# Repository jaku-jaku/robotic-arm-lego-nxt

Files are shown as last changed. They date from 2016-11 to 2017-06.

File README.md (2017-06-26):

# RoboticArm_JADO
Built a robotic arm and planetary gearbox system in 3 weeks to handle repetative tasks through joyystick training.

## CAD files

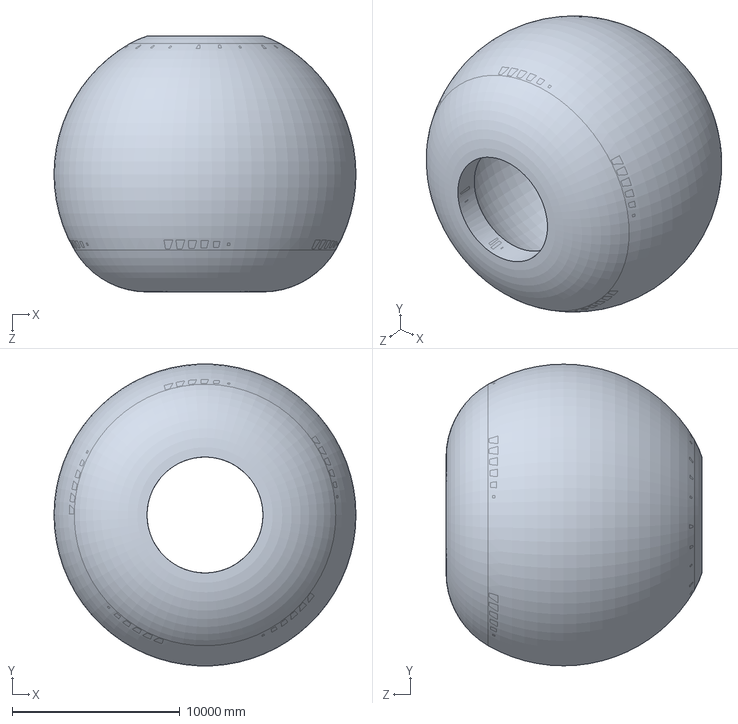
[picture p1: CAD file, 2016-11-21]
SWFiles/Boundaries.SLDPRT
17988.3 x 17970.2 x 15243.4 mm

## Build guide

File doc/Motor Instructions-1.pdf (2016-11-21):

written by Michael Stachowsky and David Lau | Page 1 of 4

# Tetrix Prime Motor Instructions

## GENE 121 – Fall 2015

### Contents

### Introduction

In this course you have access to three different motors:

1. Tetrix Prime Standard Servo – ‘S’ inscribed on servo
2. Tetrix Prime Continuous Rotation Servo – ‘C’ inscribed on servo
3. Lego NXT Motor

In order to drive or control these motors, you can use the Lego NXT brick. The Tetrix Prime servos can also be controlled with the red handheld radio controller.

### Lego NXT Brick Connections

The Tetrix Prime servos must be connected to one of the sensor ports at the bottom of the NXT brick (recommended port: S1). The Tetrix Prime servos require the NXT controller module when connecting to the NXT brick. DO NOT PLUG THE SERVO CONTROLLER INTO A MOTOR PORT, AS THIS WILL DAMAGE THE CONTROLLER (~$75).

Plug the battery pack into SV8 on the servo controller. The black wire is connected to the pin furthest

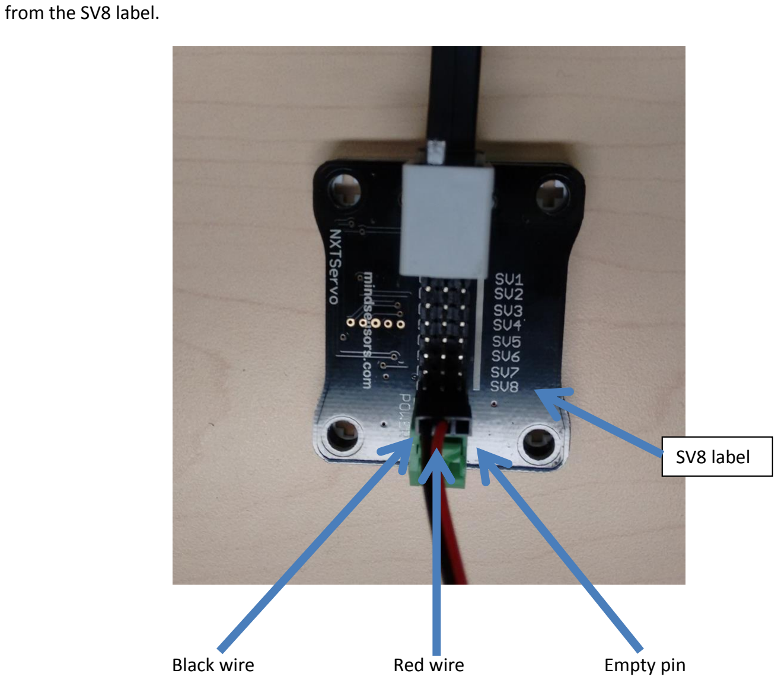
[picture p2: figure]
from the SV8 label.; Black wire; Red wire; Empty pin; SV8 label

### RobotC Code – Tetrix Prime Servos

### Library File

Download the file NXTServo-lib-UW.c into the same folder where you store your RobotC code.

### Setup Code

Your RobotC program should follow the format shown below (assuming you have plugged the interface into S1):

#include "NXTServo-lib-UW.c"

task main()
{
// configure servo controller port SensorType[S1] = sensorI2CCustom9V;

// rest of the code
}

### Continuous Servo Uncalibrated – Usage

Set the speed of the continuous rotation servos (uncalibrated), values range from -100 (counter clockwise rotation) to +100 (clockwise rotation)

setServoSpeed(int nxtPort, int servo_number,
int speed);
e.g.
// servo is plugged in to SV2, set to rotate at 45 setServoSpeed(S1, 2, 45);

// stop servo
setServoSpeed(S1, 2, 0);

### Continuous Servo – Calibration

Plug the servo to be calibrated into the servo controller port SV1. The yellow wire is connected to the pin closest to the SV1 label and the black wire is connected to the pin further from the SV1 label.

Compile and download the ServoDemo.c program to the Lego NXT robot. Run the program.

Using buttons 1 and 2 (right and left buttons) on the Lego NXT brick, increase the servo speed until the servo begins to move. Record the highest servo speed setting for which the servo does not move.

Decrease the service speed until the servo begins to move in the opposite direction. Record the lowest servo speed setting for which the servo does not move.

### Continuous Servo Calibrated – Usage

Set the speed of the continuous rotation servos (calibrated to remove the deadband)

setServoSpeed(int nxtPort, int servo_number,
int speed_setting,
int negative_offset,
int positive_offset);
e.g.
/* servo is plugged in to SV2
deadband (when then motor does not move)
is between -24 and +16
motor is set to run at 10 counts beyond the deadband */
setServoSpeed(S1, 2, 10, -24, 16);

### Standard Servo – Usage

Set the standard servo to a position between -90 degrees and +90 degrees

setServoPosition(int nxtPort, int servo_number,
int position);
e.g.
// servo is plugged in to SV4, set to 30 degrees setServoPosition(S1, 4, 30);

### Gripper – Usage

Set the gripper position from 0 to 70.

setGripperPosition(int nxtPort, int servo_number,
int position);
e.g.
// gripper is plugged in to SV5, partly open, NXT port is S1 setGripperPosition(S1, 5, 25);

To reset the gripper to its neutral position,

resetGripper(int nxtPort,
int servo_number);
e.g.
resetGripper(S1, 5); // gripper is plugged in to SV5

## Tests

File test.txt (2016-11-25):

250 0 -20 0
255 5 -20 0
260 10 -20 0
265 15 -20 0
270 20 -20 0
275 25 -20 0
280 30 -20 0
285 35 -20 0
290 40 -20 0
295 45 -20 0

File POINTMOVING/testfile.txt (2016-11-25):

6
250 0 0 0 0
260 0 0 0 0
270 0 0 0 0
280 0 0 0 0
290 0 0 0 0
300 0 0 0 0

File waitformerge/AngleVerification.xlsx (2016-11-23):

 |  |  | newX | L | alpha1 | numerator | denominator | alpha2 | alpha (rad) | alpha(deg) | alpha(rc) | RobotC Beta
100 | 100 | 100 | 141.4213562 | 173.2050808 | 0.6154797087 | -15840 | -54386.39536 | 1.275263825 | 1.890743534 | 198.3316246 | 108.33 | 45.36
200 | 100 | 100 | 223.6067977 | 244.9489743 | 0.4205343353 | -45840 | -76913.97792 | 0.932297732 | 1.352832067 | 167.5115678 | 77.51 | 77.43
300 | 100 | 100 | 316.227766 | 331.662479 | 0.3062773692 | -95840 | -104142.0184 | 0.4019963086 | 0.7082736778 | 130.5810925 | 40.58 | 126.209
400 | 100 | 100 | 412.3105626 | 424.2640687 | 0.2379411248 | -165840 | -133218.9176 | #NUM! | #NUM! | #NUM! | nan | nan
500 | 100 | 100 | 509.9019514 | 519.6152423 | 0.1936583004 | -255840 | -163159.1861 | #NUM! | #NUM! | #NUM! | nan | nan
 |  |  |  |  |  |  |  |  |  |  |  | 45.36
 |  |  |  |  |  |  |  |  |  |  |  | 45.36
 |  |  |  |  |  |  |  |  |  |  |  | 45.36
 |  |  |  |  |  |  |  |  |  |  |  | 45.36
 |  |  |  |  |  |  |  |  |  |  |  | 77.43
 |  |  |  |  |  |  |  |  |  |  |  | 126.2
 |  |  |  |  |  |  |  |  |  |  |  | nan
 |  |  |  |  |  |  |  |  |  |  |  | nan
 |  |  | numerator | denominator | beta | beta(deg) |  | 103.60 | 0
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

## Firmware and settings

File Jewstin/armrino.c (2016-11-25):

#include "NXTServo-lib-UW.c"
#include "NXT_FileIO.c"

const int GROUND_HEIGHT = -230;
const int FOREARM = 197;
const int SHOULDER = 157;
const int MAX_DIST = SHOULDER + FOREARM;
const int ALPHA_MAX = 150;
const int J3_PHYS_LIM = 90;
const int ALPHA_MIN = 60;
const int NUM_POINTS = 25;
const int GEAR_REDUCTION = 5;
const int FULL_ROTATION_EC = 360 * GEAR_REDUCTION;
const int Basketball=2;
const int Tennisball=3;
const int nothing=1;
const int football=6;

typedef struct
{
	float x , y , z;
	int gP, timeDelay; // timer will be used to control how long arm stays at each point
	bool isValid;
} Point;

typedef struct
{
	float alpha;
	float beta;
	float theta;
} AngleSet;

void readPoint(TFileHandle & in, Point & p0)
{
	readFloatPC(in, p0.x);
	readFloatPC(in, p0.y);
	readFloatPC(in, p0.z);
	readIntPC(in, p0.gP);
}

bool isZValueValid (Point p0)
{
	return (p0.z > GROUND_HEIGHT);
}

bool isWithinRange (Point p0)
{
	return (sqrt(p0.x*p0.x + p0.y*p0.y + p0.z*p0.z))	< MAX_DIST;
}


float calcAlpha(Point & input, float distanceXY, float distancePlane)
{
	float a1 = atan2(input.z,distanceXY);
	float num = (FOREARM*FOREARM) - (SHOULDER*SHOULDER) - (distancePlane*distancePlane);
	float denom = -2.0 * SHOULDER * distancePlane;
	float a2 = acos(num/denom);

	return (180.0/PI)*(a1 + a2 + PI/2.0);
}

float calcBeta(Point & input, float distancePlane)
{
	float num = (distancePlane*distancePlane) - (SHOULDER*SHOULDER) - (FOREARM*FOREARM);
	float denom = -2.0*SHOULDER*FOREARM;

	return (180.0/PI)*(acos(num/denom) - PI); //might inverst PI and acos
}

float calcTheta(Point & input)
{
	return (180.0/PI)*(atan2(input.y,input.x));
}


void calcAngleSet(Point & inputP, AngleSet & outputA)
{
	float distXY = sqrt(inputP.x*inputP.x + inputP.y*inputP.y);
	float distPlanar = sqrt(distXY*distXY + inputP.z*inputP.z);

	outputA.alpha = calcAlpha(inputP,distXY,distPlanar);
	outputA.beta = calcBeta(inputP,distPlanar);
	outputA.theta = calcTheta(inputP);
}

float min (float a, float b)
{
	if (b < a)
	{
		return b;
	}

	return a;
}

float calcMaxBeta (AngleSet & a0)
{
	float beta = 180-a0.alpha;
//	displayString(0,"%0.2f", beta);
	return min(beta, J3_PHYS_LIM);
}

bool anglesValid (AngleSet & a0)
{
	bool output;
	if (a0.alpha <=ALPHA_MAX && a0.alpha >= ALPHA_MIN)
	{

		if (!(a0.beta < calcMaxBeta(a0)))
		{
			eraseDisplay();
		}
		else
		{
			output = true;
		}
	}
	else
	{
		output = false;
	}
	return output;
}

bool isPointValid(Point & p0, AngleSet & a0)
{
	//is point close enough to be able to be reached
	//check z value above the grounnd isZValueValid fun
	bool output = false;

	if (isWithinRange (p0) && isZValueValid (p0))
	{
		calcAngleSet(p0,a0); // calculates all 3 angles

		if (anglesValid (a0) == true)
		{
			output = true;
		}

		//is alpha within range
		//is beta within range
		//if all of the above are okay, then go ahead and move.
	}
	return output;
}
int getEC(){
	int ECvalue=nMotorEncoder[motorA]%FULL_ROTATION_EC;
	//displayString(1,"%f",ECvalue);
	if(ECvalue<0){
		ECvalue+=FULL_ROTATION_EC;
	}
//	displayString(2,"%f",ECvalue);
	return ECvalue;
}
//Testing
int smoothMotionFunc(float index0, int MAXspeed0,int MINspeed0){
	float percent=0;
	if(index0>1){
		percent=1;
	}else
		percent=1/(1+pow(10,(2-4*index0));

	return ((int)((MAXspeed0-MINspeed0)*percent)+MINspeed0);
	//y=1/(1+10^(2-4x))
	//On theory accelerate 0-1 in 0-1
	//and after x=1, y->1
	//so for computation, we do not need to calculate input after x=1
}

int smoothMotion(int curECdif, int initialECDiff){
	int MAXspeed=70,MINspeed=10;
	float index=0, ANGLECHANGE=40;
	//20 degree for changing speed
	index=curECdif;
	if(curECdif>initialECDiff/2.0){
		index=initialECDiff-index;
		//reverse at middle of the action to gain slow down in the end
	}
	index=index/(ANGLECHANGE*5);
//		displayString(2,"%f",index);
	return smoothMotionFunc(index, MAXspeed,MINspeed);
}
void moveJoint1(float ang)
{
	//V1
	//displayString(5,"%i",getEC());
	//int power=20;
	//if(ang<0)
	//	ang+=360;
	//// might need to fix for going backwards direction
	//int targetEC = (int)(ang*FULL_ROTATION_EC/360.0);
	//int forward=1,cw=1;//1 f/ -1 b
	////displayString(6,"%i",targetEC);
	//int diff=targetEC-getEC();

	//	forward=1;
	//	cw=1;
	//	diff=targetEC-getEC();
	//	if(abs(diff)>FULL_ROTATION_EC/2.0){
	//		forward=-1;
	//	}
	//	if(diff>0){
	//		cw=-1;
	//	}
	//		//displayString(7,"%i",getEC())
	//	wait1Msec(2000);
	//	motor[motorA] = -1*power*cw*forward;
 // while(diff!=0){
 // 	diff=targetEC-getEC();
 // 	//displayString(7,"%i",getEC());
 // 	//	while(nNxtButtonPressed!=-1){
	//		//			motor[motorA]=0;
	//		//}

 // 	}
	//motor[motorA] = 0;

///----
	int power=20;
	if(ang<0)
		ang+=360;
	// might need to fix for going backwards direction
	int targetEC = (int)(ang*FULL_ROTATION_EC/360.0);
	int forward=1,cw=1;//1 f/ -1 b
	//displayString(6,"%i",targetEC);
	int diff=targetEC-getEC();
	int initDiff=diff;
	//	displayString(7,"%i",getEC());
	//	wait1Msec(2000);
	while(diff!=0){
		forward=1;
		cw=1;
		if(abs(diff)>FULL_ROTATION_EC/2.0){
			forward=-1;
		}
		if(diff>0){
			cw=-1;
		}
			//displayString(7,"%i",getEC());
			power=smoothMotion(fabs(initDiff-diff),fabs(initDiff));
		motor[motorA] = -1*power*cw*forward;
  	diff=targetEC-getEC();
  //	displayString(7,"%i",getEC());
  	if(diff==0){
  			motor[motorA] = 0;
  			//wait1Msec(200);
  			//diff=targetEC-getEC();//PD not working
  	}
  }
	motor[motorA] = 0;

	////----

	//if (targetEC > nMotorEncoder[motorA])
	//{
	//	motor[motorA] = 40;
	//	while(nMotorEncoder[motorA] < targetEC) {}
	//}
	//else if (targetEC < nMotorEncoder[motorA])
	//{
	//	motor[motorA] = -40;
	//	while (targetEC > nMotor
	//}






	//motor[motorA] = 40;
	//while (nMotorRunState[motorA] != runStateIdle) {}
	//motor[motorA] = 0;
}

void moveJoint2(float ang)
{
	setServoPosition(S4, 1, 0.0014*ang*ang +1.5288*ang - 173.79 );   // QUAD: 0.0014*ang*ang +1.5288*ang - 173.79
}

void moveJoint3(float ang)
{
	setServoPosition(S4, 2, -0.0007*ang*ang + 0.9882*ang + 21.773); // -0.0007*ang*ang + 0.9882*ang + 21.773
}

void moveRobot(AngleSet & a0)
{
	moveJoint2(a0.alpha);
	moveJoint3(a0.beta);
	moveJoint1(a0.theta);

}

void gripperController(int angle){	//0 closed, 180 open
	if (angle>=0||angle<=180)
		setServoPosition(S4, 3, angle);
}
void gripperBalls(){
	//nxtDisplayCenteredTextLine(3, "%f",SensorValue[S2] );
	if(SensorValue[S2]==nothing||SensorValue[S1]==1)
		gripperController(90);
	else{
		gripperController(8);
	}
}

task main()
{
	// zero encoder as well after calibration

	SensorType[S1] = sensorTouch;
	SensorType[S2] = sensorColorNxtFULL;
	SensorType[S3] = sensorSONAR;
	SensorType[S4] = sensorI2CCustom9V;

	nMotorEncoder[motorA] = 0;
	clearTimer(T1);

	short amplitude = 45;
	while (nNxtButtonPressed == -1);
	displayString(0, "Button Pressed");
	wait1Msec(1000);
	clearTimer(T1);
	while (nNxtButtonPressed == -1)
	{
		displayString(1, "%d", time1[T1];
		wait1Msec(100);
	}
	displayString(0, "Button pressed");

	wait1Msec(1000);
}

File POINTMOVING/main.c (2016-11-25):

#include "definitions.h"

//---------------------//
//---Button Function---//
//---------------------//
//general btn function
void waitBtn(){
	while(nNxtButtonPressed==-1){}
	while(nNxtButtonPressed!=-1){}
}
void waitAndContinue(){
	displayString(3,"Starts in 5 seconds");
	displayString(4,"Step back!");
	//Give 5 seconds for operator leaving the platform
	for(int i=0;i<5;i++){
		PlaySound(soundBeepBeep);
		wait1Msec(1000);
	}
	ClearSounds();
	playSoundFile("Warnning.rso");
	wait1Msec(1000);
	eraseDisplay();
}



task stopIfUnsafe()
{
	while (SensorValue[S_TOUCH] == 0)
	{
		gripperController(90);
		EndTimeSlice();
	}

	stopAllTasks();
}

task main()
{

	//---initialization---//
	SensorType[S_TOUCH] = sensorTouch;
	SensorType[S_COLOR] = sensorColorNxtFULL;
	SensorType[S_ULTRA] = sensorSONAR;
	SensorType[S_SERVO] = sensorI2CCustom9V;

	StartTask(stopIfUnsafe);
	//Declare Variables
	int QUANTITY;//from first line from input file
	int pointer=0;
	int cnt=0,QUANleft=0;
	Point listOfPoints[MAX];
	AngleSet listOfAngles[MAX];

		for (int i = 0; i < MAX; i++)
		{
			// account for (0,0,0) case
			listOfPoints[i].x = 1;
			listOfPoints[i].y = 1;
			listOfPoints[i].z = 1;
			listOfPoints[i].gP = 0;
			listOfPoints[i].isValid = false;
			listOfAngles[i].alpha = 0;
			listOfAngles[i].beta = 0;
			listOfAngles[i].theta = 0;
		}

	//Check IF File open
	TFileHandle fin;
	bool isFileOk = openReadPC(fin,"testfile.txt");
	//ReadFile && Assign 20 coordinates
	if(isFileOk)
		readIntPC(fin, QUANTITY);
	if (!isFileOk&&QUANTITY<=0)
		displayString(0,"ERROR! File");
	else{//whole program
		//-BEGIN- Auto-Calibrating joint1
		nxtDisplayCenteredTextLine(0, "Calibrate!");
		displayString(2,"Press Any Button");
		displayString(3,"to begin");
		waitBtn();//Wait for starting the program
		eraseDisplay();
		nxtDisplayCenteredTextLine(0, "Caution");
		waitAndContinue();//safe waiting function
		nxtDisplayCenteredTextLine(0, "Operating");
		wait1Msec(2000);
		displayString(2,"caution");//ex
		zeroZAxis();
		//-END- of auto-calibration


		//-BEGIN- start to performing
		PlaySound(soundBeepBeep);
		nxtDisplayCenteredTextLine(0, "System Ready");
		displayString(2,"GIVE THE BALL");
		displayString(3,"TO THE ROBOT!");
		gripperController(90);
		while(SensorValue[S_COLOR]==nothing)
		{};
		eraseDisplay();
		waitAndContinue();
		//---READY File input---//
		QUANleft=QUANTITY;
		while(cnt<QUANTITY)
		{
			pointer=0;
			for(int i=0;i<MAX&&i<QUANleft;i++)
			{
				readPoint(fin,listOfPoints[i]);
				pointer++;
				cnt++;
			}

			//---MASSAGE Input---//
			//Manipulating class - Converting points to joint angle and Validate if the point reachable
			for(int i=0;i<MAX&&i<QUANleft;i++)
			{
				listOfPoints[i].isValid = isPointValid(listOfPoints[i],listOfAngles[i]);
			}
			//--ACTION--//
			for(int i=0;i<MAX&&i<QUANleft;i++)
			{
				displayString(0,"%i",i);
				displayString(1,"x: %f",listOfPoints[i].x);
				displayString(2,"y: %f",listOfPoints[i].y);
				displayString(3,"z: %f",listOfPoints[i].z);
				if (listOfPoints[i].isValid)
				{
					moveRobot(listOfAngles[i]);
					displayString(4,"Alpha %d", listOfAngles[i].alpha);
					displayString(5,"Beta %d", listOfAngles[i].beta);
					displayString(6,"Theta %d", listOfAngles[i].theta);
					wait1Msec(listOfAngles[i].tMsDelay);
				}//END-if
				else{
					eraseDisplay();
					nxtDisplayCenteredTextLine(0, "ERROR");
					displayString(2,"Do you want to");
					displayString(3,"skip and continue");
					//displayString(4,"??? Any Button");
					PlaySound(soundBeepBeep);
					while(nNxtButtonPressed==-1){}//END while-bt
					ClearSounds();
					while(nNxtButtonPressed!=-1){}
					wait1Msec(500);
					eraseDisplay();
					displayString(4,"NEXT");
					//waitAndContinue();
				}//END-else

			}//END-for
		 QUANleft-=MAX;
		}//END-while
	}

}

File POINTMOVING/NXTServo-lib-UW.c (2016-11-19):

/**********************************************************************
Filename: NXTServo-lib-UW.c
Date: June 6, 2015
File Version: 1.3

A wrapper for the drivers provided by Mindsensor for use with the
NXTServo interface module.

History
Ver  Date       Comment
1.4  Jun  6/15  included code from NXTServo-lib.c (which was updated for
                parameter passing in RobotC v4.30); removed fixed deadband
                correction since it is different for each motor; reduced maximum
                gripper angle by 5 degrees;
1.3  Jan 15/15  changed offset values and scaling
1.2  Jan 14/15  scaled speed setting by 4. previous range from -100 to 100.
                updated range now -400 to 400 with the function call range
                still -100 to 100.
1.1  Jan 12/15  restrict to valid servo numbers 1-7; added SetGripperPos
                to limit gripper servo position;  limit servo position
                to 0 to 180; added constants, valid setting function,
                parameter check function;
                generalized to use any NXT sensor port;
1.0  Dec 18/14  original release

**********************************************************************/
/*
NXTServo-lib.c
This is function library to use with mindsensors.com NXTServo module.
For use with RobotC.
V1.0
2008(c) mindsensors.com
for more info visit www.mindsensors.com

History:
When           Ahthor/Editor          Comments
06/06/15       C. Hulls               Convert I2C functions to pass pointers to message arrays;
                                      Removed extra ; from empty loopsl
05/29/08       Deepak Patil           Initial creation of the file.
03/21/11       support                Added support for Port and i2c address in API parameters
*/

/**********************************************************************
NXTServo-lib.c
**********************************************************************/
/*===========================================================================
Register Summary
===================
Register Read Operation                       Write Operation
0x00    sw version                            control reg

0x01    Servo 1 speed                         Servo 1 speed
0x02    Servo 1 Position low byte in uS	      Servo 1 Position low byte in uS
0x03    Servo 1 Position hi byte in uS	      Servo 1 Position hi byte in uS

0x04    Servo 2 speed                         Servo 2 speed
0x05    Servo 2 Position low byte in uS	      Servo 2 Position low byte in uS
0x06    Servo 2 Position hi byte in uS	      Servo 2 Position hi byte in uS

0x07    Servo 3 speed                         Servo 3 speed
0x08    Servo 3 Position low byte in uS	      Servo 3 Position low byte in uS
0x09    Servo 3 Position hi byte in uS	      Servo 3 Position hi byte in uS

0x0a    Servo 4 speed                         Servo 4 speed
0x0b    Servo 4 Position low byte in uS	      Servo 4 Position low byte in uS
0x0c    Servo 4 Position hi byte in uS	      Servo 4 Position hi byte in uS

0x0d    Servo 5 speed                         Servo 5 speed
0x0e    Servo 5 Position low byte in uS	      Servo 5 Position low byte in uS
0x0f    Servo 5 Position hi byte in uS	      Servo 5 Position hi byte in uS

0x10    Servo 6 speed                         Servo 6 speed
0x11    Servo 6 Position low byte in uS	      Servo 6 Position low byte in uS
0x12    Servo 6 Position hi byte in uS	      Servo 6 Position hi byte in uS

0x13    Servo 7 speed                         Servo 7 speed
0x14    Servo 7 Position low byte in uS	      Servo 7 Position low byte in uS
0x15    Servo 7 Position hi byte in uS	      Servo 7 Position hi byte in uS

0x16    Servo 8 speed                         Servo 8 speed
0x17    Servo 8 Position low byte in uS	      Servo 8 Position low byte in uS
0x18    Servo 8 Position hi byte in uS	      Servo 8 Position hi byte in uS

0x19    battery voltage	None


================
Psudo registers
================

0x1A			servo position 1			nothing
0x1b			servo position 2			nothing
0x1c			servo position 3			nothing
0x1d			servo position 4			nothing
0x1e			servo position 5			nothing
0x1f			servo position 6			nothing
0x20			servo position 7			nothing
0x21			servo position 8			nothing

*/

#pragma SystemFile

const int kSc8CommandReg    = 0x41;
const int kSc8_speed        = 0x52;
const int kSc8_lowbyte      = 0x42;
const int kSc8_hibyte       = 0x43;

const int kSc8_Vbatt        = 0x41;


/**********************************************************************
UW code
**********************************************************************/

// available servo numbers
const int MIN_SERVO_NUM = 1;
const int MAX_SERVO_NUM = 7;  // assumes SV8 used for power

// continous servo
const int MAX_SERVO_SPEED = 100;  // max at +/- 100
const int SERVO_NEUTRAL = 1550;  // 1550 us is neutral position (off)

// standard servo position limits
const int MIN_SERVO_ANGLE = 0;  // numbers are from datasheets, verified w/ servo
const int MAX_SERVO_ANGLE = 180;
const int SERVO_OFFSET = 90;  // make zero to be the neutral position
const int SERVO_ZERO = 600;  // 600 us is 0 angle for servo
const int MIN_GRIP_ANGLE = 50;  // numbers are based on tests with gripper
const int MAX_GRIP_ANGLE = 120;

// default I2C address (factory setting)
const int I2C_ADDR = 0xb0;

// control register
const ubyte CONTROL_REG_ADDR = 0x41;

/**********************************************************************
NXTServo-lib.c
**********************************************************************/

/*===================================
**
** Read the battery voltage data from
** NXTServo module (in mili-volts)
**
===================================*/
int  NXTServo_Get_Batt_V(tSensors kSc8Port, int kSc8ID)
{
	ubyte sc8Msg[5];
	const int kMsgSize       = 0;
	const int kSc8Address    = 1;
	const int kReadAddress   = 2;
	ubyte replyMsg[2];

	// Build the I2C message
	sc8Msg[kMsgSize]         = 2;
	sc8Msg[kSc8Address]      = kSc8ID ;
	sc8Msg[kReadAddress]     = kSc8_Vbatt ;

	while (nI2CStatus[kSc8Port] == STAT_COMM_PENDING)  // CH removed ;
	{
		// Wait for I2C bus to be ready
	}
	// when the I2C bus is ready, send the message you built
	sendI2CMsg(kSc8Port, &sc8Msg[0], 1);  // CH added &

	while (nI2CStatus[kSc8Port] == STAT_COMM_PENDING)  // CH removed ;
	{
		// Wait for I2C bus to be ready
	}
	// when the I2C bus is ready, send the message you built
	readI2CReply(kSc8Port, &replyMsg[0], 1);  // CH added &

	return(37*(0x00FF & replyMsg[0]));  // 37 is calculated from

	//supply from NXT =4700 mv /128
}
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

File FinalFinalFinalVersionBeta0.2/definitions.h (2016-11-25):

//PORT I/O assigning
const int S_COLOR = S2;
const int S_ULTRA = S3;
const int S_TOUCH = S1;
const int S_SERVO = S4;
const int J1 = motorA;
const int J2 = 1;
const int J3 = 2;
const int GRIPPER = 3;
const int MAX = 8;
//ROBOT MECHANICAL DATA
const int GROUND_HEIGHT = -230;
const int FOREARM = 197;
const int SHOULDER = 157;
const int MAX_DIST = SHOULDER + FOREARM;
const int ALPHA_MAX = 150;
const int J3_PHYS_LIM = 90;
const int ALPHA_MIN = 60;
const int NUM_POINTS = 10;
const int GEAR_REDUCTION = 5;
const int FULL_ROTATION_EC = 360 * GEAR_REDUCTION;
//colorSensorValue
const int Basketball=2;
const int Tennisball=3;
const int nothing=1;
const int football=6;

typedef struct
{
	float x;
	float y;
	float z;
	int tMsDelay;
	int gP;//Gripper Position
	bool isValid;
} Point;

typedef struct
{
	float alpha;
	float beta;
	float theta;
	int tMsDelay;
	int gP;//Gripper Position
	bool isValid;
} AngleSet;

//FileIO
// Ali Toyserkani
void readPoint(TFileHandle & in, Point & p0);
//AngleValidation
// Oswaldo Ferro Hernandez
bool isZValueValid (Point p0);
bool isWithinRange (Point p0);
bool isPointValid(Point & p0, AngleSet & a0);

//AngleCalculation
//Dustin Hu
float calcAlpha(Point & input, float distanceXY, float distancePlane);
float calcBeta(Point & input, float distancePlane);
float calcTheta(Point & input);
void calcAngleSet(Point & inputP, AngleSet & outputA);

// Oswaldo Hernandez
float min (float a, float b);
float calcMaxBeta (AngleSet & a0);
bool anglesValid (AngleSet & a0);
int getEC();
// Jack Xu
int smoothMotionFunc(float index0, int MAXspeed0,int MINspeed0);
int smoothMotion(int curECdif, int initialECDiff);
void moveJoint1(float ang);

// Dustin Hu
void moveJoint2(float ang);
void moveJoint3(float ang);
void moveRobot(AngleSet & a0);

// Jack Xu
void gripperController(int angle);
void gripperBalls();
void waitBtn();
void waitAndContinue();

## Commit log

2016-11-17 robotic arm sketch
2016-11-17 basic frame
2016-11-18 Add files via upload
    Servo Testing - done
    zero z axes - perfect
    - things need to improve: PD sigmoid control to increase precision && get mean average data and do second test to increase the accuracy of 0ing
2016-11-18 Definitions
    A couple functions written
2016-11-18 Removed Atan2()
    Removed atan2(); Professor Hulls told me that atan2() is implemented in
    RobotC
2016-11-19 Alphas work!
    calcAlpha() works. CalcBeta().... Sort of works.
    Setting angles does not work. A function to translate it into motor
    movements is needed.
    [NXTServo-lib-UW.c, definitions.c, definitions.h]
2016-11-20 Verified angles
    Verified that angle calculations work
    Got angle validations down.
    [AngleVerification.xlsx]
2016-11-20 MoveJ2()
    Modelled movement at J2 with a quadratic; the quadratic produces a much
    closer to reality approximation than the linear approximation
    [AngleVerification.xlsx]
2016-11-20 Moved Oswaldo's code into here
    Moved Oswaldo's code into here, changed a couple variables a bit.
2016-11-20 US and Touch Consistent Safety Checks (minus accounting for during calibration)
2016-11-21 Arm Range
    [Boundaries.SLDPRT]
2016-11-21 Servo Commands
2016-11-22 Testing
    Testing some more
    [AngleVerification.xlsx]
2016-11-23 Fixed angles
    Fixed angle calculations; accounted for missing distances
    [AngleVerification.xlsx]
2016-11-23 7Files - Z axis rotation code fix and work
    [definitions.c, definitions.h]
2016-11-23 Fixed newX's
    Jack broke my newX's.
    He deleted them all.
    [definitions.c, definitions.h]
2016-11-23 Fixed some more stuff
    Fixed some more stuff that was broken in Jack's commit
    [definitions.c, testMain.c]
2016-11-23 Fixed moveJ2()
    Changed the formula for moveJ2 by plotting more pointns and using excel
    again
    [AngleVerification.xlsx]
2016-11-23 Updated moveJ3()
    MoveJ3() quadratic changed a bit
    [AngleVerification.xlsx]
2016-11-23 ConvEncoderValue
    ADded a function to convert an angle to an encoder value
2016-11-24 Final Code For Movement (minus debudding minor issues)
    [RobotArmMovementFile.c]
2016-11-25 added set servo position
2016-11-25 Added abortion
    Aborts task if button pressed

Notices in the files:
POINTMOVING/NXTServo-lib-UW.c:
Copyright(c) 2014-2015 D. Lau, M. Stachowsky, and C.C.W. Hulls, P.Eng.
